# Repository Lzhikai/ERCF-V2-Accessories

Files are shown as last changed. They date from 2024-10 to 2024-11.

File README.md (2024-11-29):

# ERCF-V2-Accessories
 - [ERCF_v2-Official link](https://github.com/Enraged-Rabbit-Community/ERCF_v2)
 - [Siboor-ERCF_v2 kit Document link](https://docs.siboor.com/siboor-ercf-v2)  

## Announcement
In compliance with the latest requirements from the ERCF V2 team, the SIBOOR ERCF V2 GitHub repository will only host STL files created or modified by SIBOOR. For all other STL files, please download them from the official ERCF V2 platform.
To help our users better understand which STL files they need, we’ve prepared a concise guide. We hope it will be helpful to you!
Thank you for your support!  
https://docs.siboor.com/siboor-ercf-v2/the-build/1print-necessary-parts

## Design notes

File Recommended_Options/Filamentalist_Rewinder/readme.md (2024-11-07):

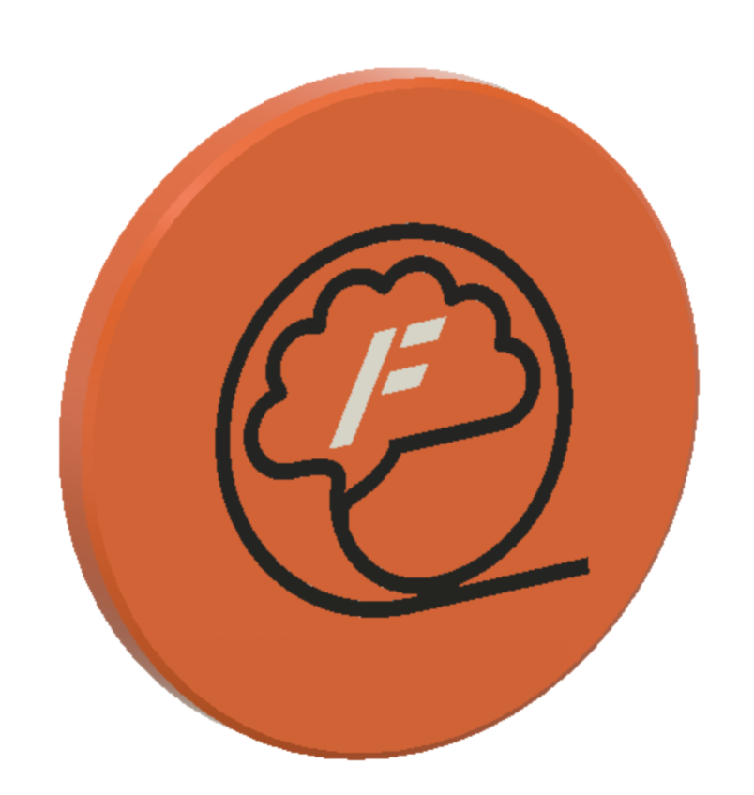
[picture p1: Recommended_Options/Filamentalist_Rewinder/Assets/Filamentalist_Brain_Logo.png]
<h1 align="center">The "Filamentalist"      Passive Filament Driven Rewinder</h1>
<p align="center">
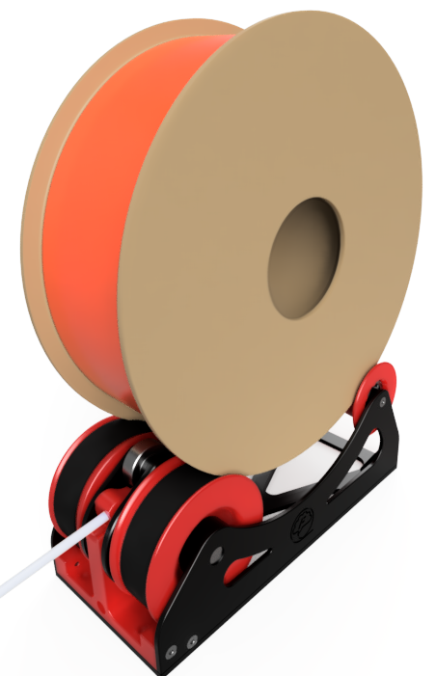
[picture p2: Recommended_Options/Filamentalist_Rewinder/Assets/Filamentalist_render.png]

</p>

## Filamentalist Discord group [here:](https://discord.gg/uDcGxukRKd) ##

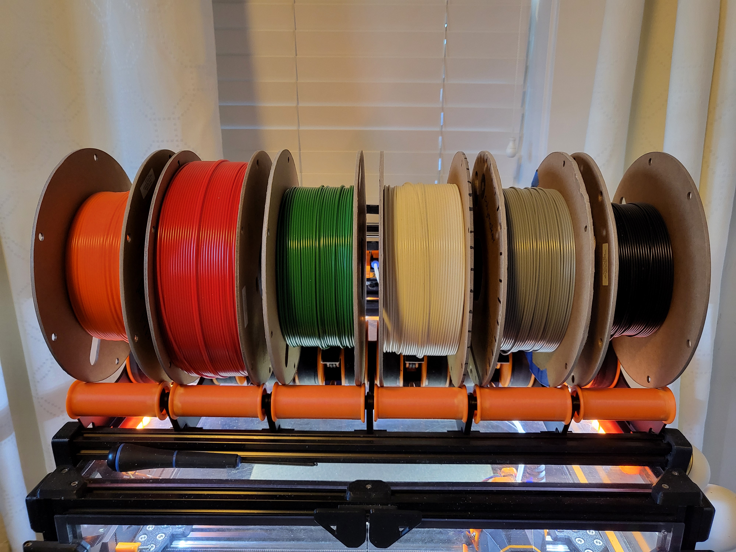
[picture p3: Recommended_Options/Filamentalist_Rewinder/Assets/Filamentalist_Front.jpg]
<p align="center">
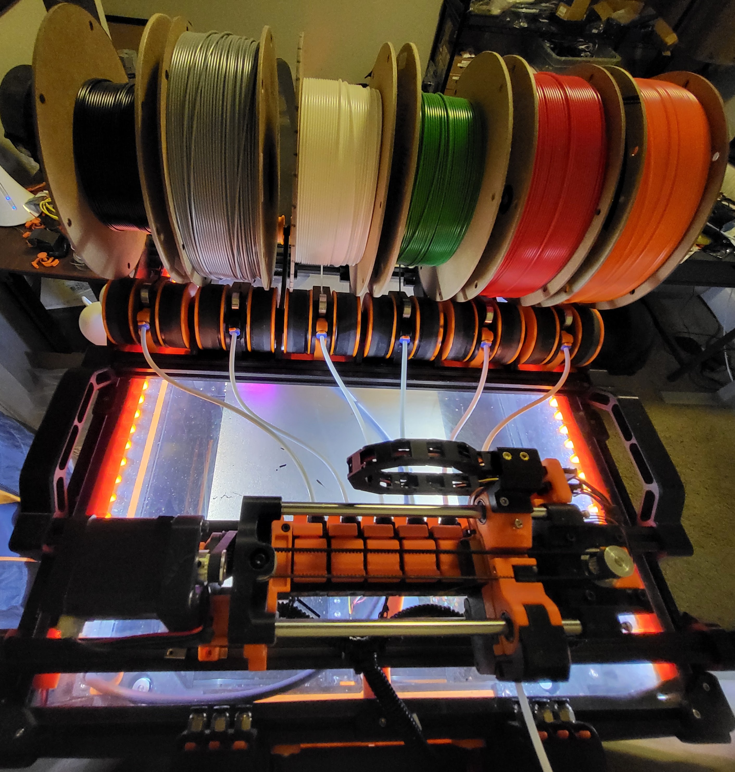
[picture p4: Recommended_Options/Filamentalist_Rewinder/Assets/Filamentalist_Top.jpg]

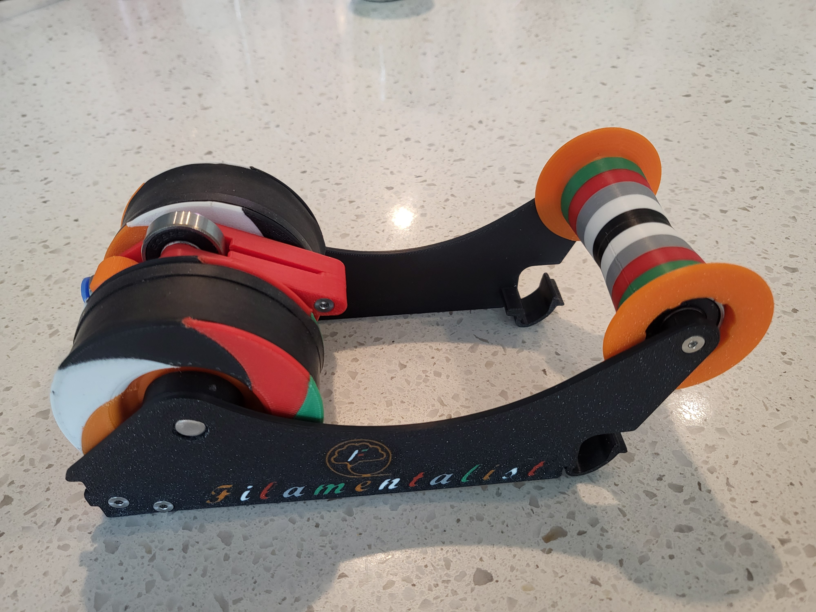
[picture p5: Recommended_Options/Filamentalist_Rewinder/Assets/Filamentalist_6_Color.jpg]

</p>

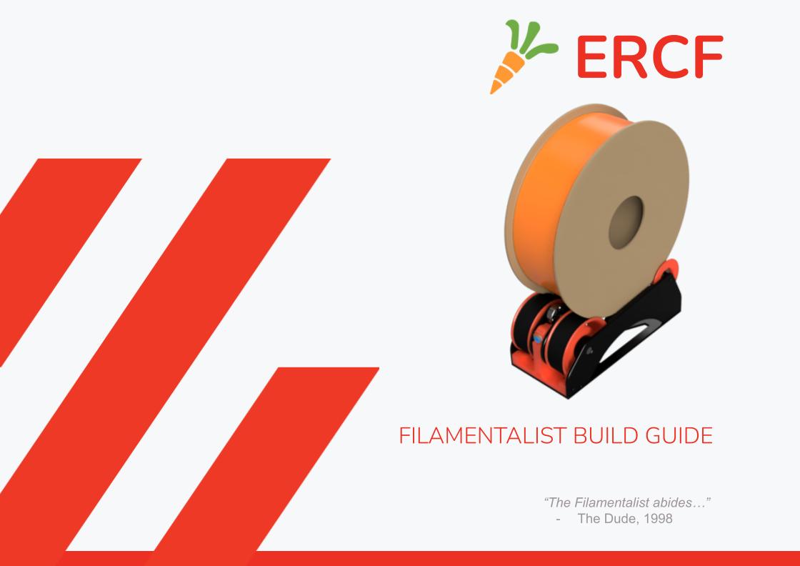
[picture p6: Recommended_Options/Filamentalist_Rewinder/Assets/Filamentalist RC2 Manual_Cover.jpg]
## [Filamentalist Assembly Guide Document](https://github.com/Enraged-Rabbit-Community/ERCF_v2/blob/b04e75d1da1841365e015c20a97aaef5a365349d/Recommended_Options/Filamentalist_Rewinder/Documentation/Filamental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)  [](https://github.com/Enraged-Rabbit-Community/ERCF_v2/blob/master/Recommended_Options/Filamentalist_Rewinder/Documentation/Filamentalist_Rewinder_Manual_V3.pdf)

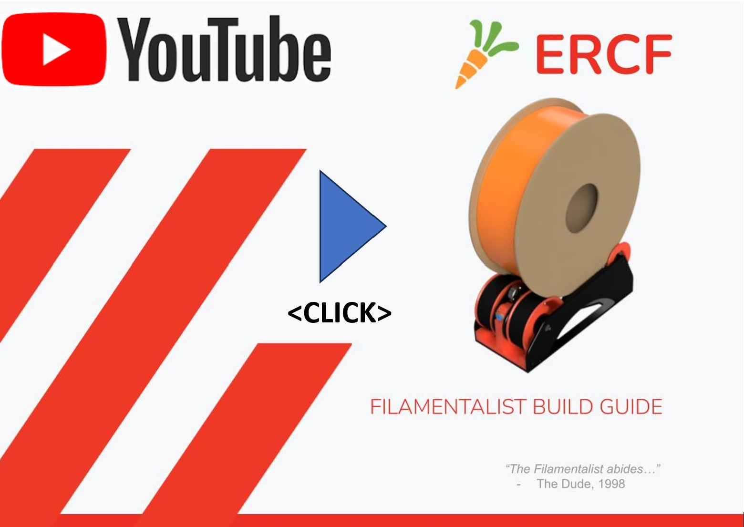
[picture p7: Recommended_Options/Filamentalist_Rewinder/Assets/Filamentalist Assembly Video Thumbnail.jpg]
## [Filamentalist Assembly Guide Video](https://youtu.be/-1cHOcnosxE?si=RZV318OI9f3f_CkE)  [](https://youtu.be/-1cHOcnosxE?si=RZV318OI9f3f_CkE)

## Video of 6 rewinders swapping (plus SW Only Blobifier Purging):  [](https://photos.app.goo.gl/hKso7JYPZcdRLKrW8)

## [Video of loading a spool (pre-gate sensors auto-detect filament and pull into ERCF):](https://photos.app.goo.gl/qPX1pxYLU2VeUuqV8)  [](https://photos.app.goo.gl/qPX1pxYLU2VeUuqV8)

## [Filamentalist Enclosure Drybox Project Github](https://github.com/SkiBikePrint/ERCF_Mods/tree/main/Filamentalist_Enclosure)
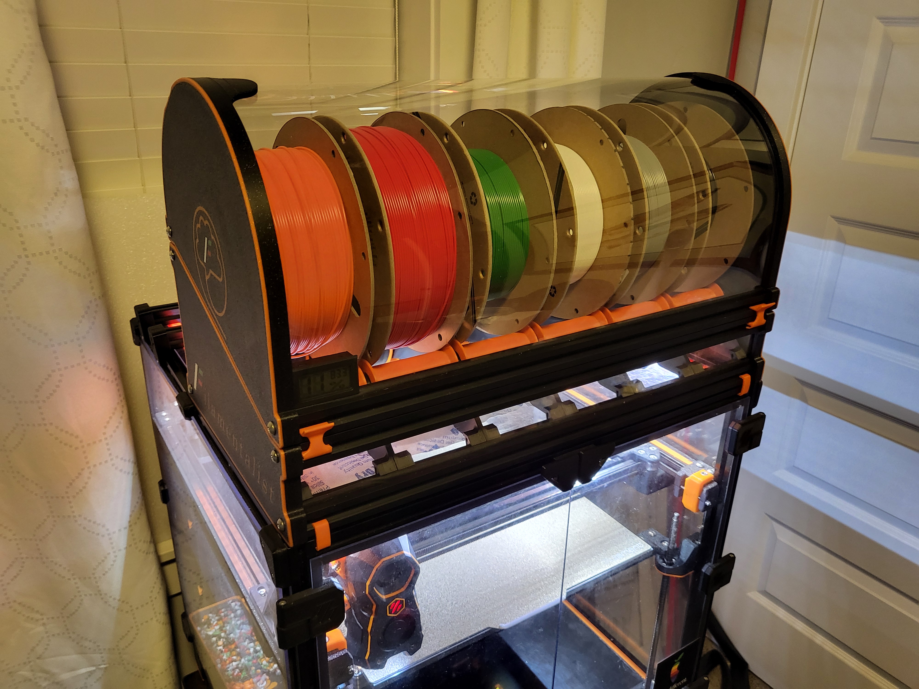
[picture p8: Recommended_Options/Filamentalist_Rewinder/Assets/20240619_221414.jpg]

</p>

##  Theory of operation:

The Filamentalist is an integrated solution for buffering and spool holding providing space savings as well as the potential for filament path reduction and the associated drag/resistance that comes with long runs from spool to buffer to MMU.

- The Filamentalist uses the axial force delivered by the MMU gear motor along the filament to load and unload to and from the filament spool.
- An adjustable spring clamp forces the filament against two o-rings that sit on the drive pulley to create a high traction interface for rotating the axle and filament spool.
- A one-way clutch style bearing locks against the drive shaft and rotates the filament spool to take up filament during an unload.
- For loading and print extruding, the clutch disengages allowing for effective free-spooling of the filament spool similar to a roller style spool holder.
- The difference in diameter of the filament driven clutched roller versus the larger roller that the filament spool sits on provides the needed gear ratio to produce enough rotations to take up, and unload a nearly empty or full filament roll.
- During unloading/buffering, to account for the varying diameter of a spool from full to empty filament tension will cause the spring loaded arm to lift a small amount and release traction from the o-rings allowing slip to occur between the filament and the o-ring interface of the rewinder (full spool = max slip, empty spool = no/minimal slip).

<p align="center">
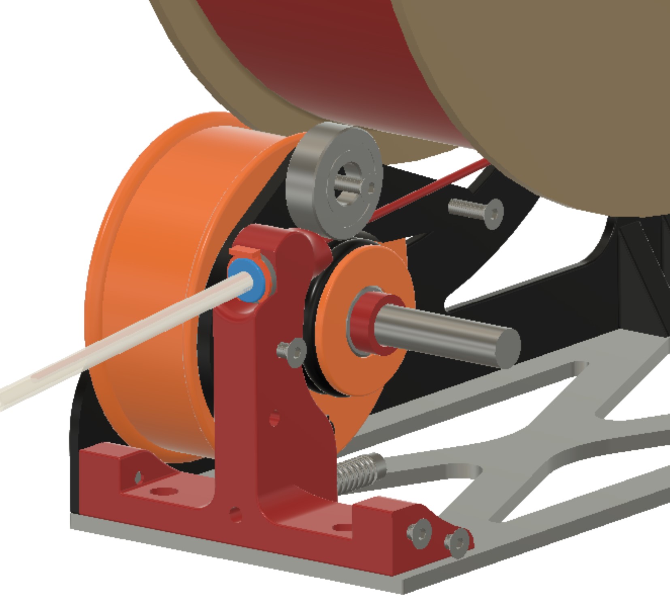
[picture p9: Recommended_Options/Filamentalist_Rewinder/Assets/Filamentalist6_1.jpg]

</p>

##  Credits:
Discord user Thisiscam first made me aware of [Muzi Xiaoyang's video](https://www.bilibili.com/video/BV1ZM41197fX/?spm_id_from=333.337.search-card.all.click) of a filament driven rewinder .  Through a long collaboration with Thisiscam, a great Beta dev/test team, and many design iterations/improvements on the Muzi Xiaoyang design, the Filamentalist was born. Key changes to the Muzi Xiaoyang design include incorporation of a one-way bearing, establishing the correct gear ratio for operation across the range of empty-to-full spools, and the long-life o-ring based filament clamping interface.

A special mention and thanks goes out to Cheesefrog and JCPhlux for their innovation and inputs for design refinement. 

##  **Additional Notes/Considerations** 

Things that you need to know include:
1. Due to continual evolution of the design based on user feedback, the pictures in this guide may not reflect the most current design.  They will be similar and generally represent the latest parts and assemblies .  The part names in the Printing Guidelines below will be kept current to match the CAD/STL files.
2. There are multiple options for the Filamentalist.  Determine which versions/options you want and select the stl's to print accordingly.
   - Unit Width: 80mm, 100mm, and custom width via Fusion 360 parametric model
     -  80mm - Designed around 80mm long off-the-shelf 8mm axles.  This standard version maximizes space efficiency with common spool size compatibility, accomodating spool widths up to 68mm.  Total rewinder width is 81.5mm allowing 6 units across the top of a 350 Voron mounted on 500mm extrusions.
     -  100mm - Designed around 100mm long off-the-shelf 8mm axles.  This size accomodates spool widths up to 86.5mm (basically all brands of 1kg spools).  Total rewinder width is 100mm.
     -  Parametric Model - If you use Autodesk Fusion 360 you can adjust the design for virtually any realistic spool width and axle size.  You can also "push" the design a bit using an acceptable axle "underhang" to get more spool width.  For example you can effectively accomodate a spool width of 72mm (KVP, NinjaFlex) on the 80mm axle with an underhang value of -2.75mm.  With this underhang the axle is still fully captured by the 608 bearings.  You could even push this further to an underhang of -5.75mm to get a max spool width of 78mm and still have acceptable axle engagement with the 608 bearings.
   - Mounting Style: Standard (shelf) mount, 2020 rail clip-in mount, 2020 clip-in mount for Filamentalist Enclosure
       - Based on your mounting needs, you may or may not need to print and install the Base Plate part.  It is really only needed if you don't plan to attach the rewinder to a surface.
   - Feed Direction: The orientation of your MMU with respect to your filament spools location may require a front, rear, or bottom loading capability from the
       rewinder.  Tensioner Mount options are provided to support this.
   - Pre-gate Sensors: If your MMU does not have pre-gate sensors and the software you use supports them (like Happy Hare) there are Tensioner Mount options that  support this.
3. If you're using, or upgrading from a ERCFv1 or v2 RC1A version you may want/need a higher torque gear motor.  Many in the Beta team ran NEMA 17's spec'd at 55 N-cm max torque and config'd them for 1-1.5A (probably overkill...).  Grafton's [40 Tooth NEMA 17 Mod](https://www.printables.com/model/692720-ercf-40-tooth-gear-modifiction) is a good addition for gaining more speed from a high torque motor.  This may not be required so if you already have built your ERCF, try the Filamentalist with the motor/gearing you have and decide if you think you need more torque/speed.
4. One baseline width of the Filamentalist is set to use a 80mm axle length.  It has a maximum spool width of 68mm and supports most standard 1, 0.5, and 0.25KG spool sizes and still be able to fit 6 rewinders across the top of a 350 size Voron printer. Height was set to be as low as possible to fit some existing dry box designs although there is the possibility to make user modifications to to reduce height further if needed. Some spools such as NinjaFlexand KVP's are too wide to fit the 80mm design.  If you use spools wider than 68mm there is also step and stl files posted for a 100mm axle length version. If you are using Autodesk Fusion 360 the provided .f3d file in the CAD directory is a parametric based model allowing you to customize the width of your rewinder to suit your max/min spool widths and/or to design around a standard available steel axle length (see instructions here  [parametric_model](https://github.com/Enraged-Rabbit-Community/ERCF_v2/blob/master/Recommended_Options/Filamentalist_Rewinder/CAD/readme.md) ). 
5. Because the standard tuning of this design relies on some filament slip at the o-rings, the o-rings may ultimately wear-out.  Testing and extrapolation estimates that the wear-out point is ~5K cycles. See the O-Ring Replacement section at the end of this document for o-ring swap/replacement instructions. 
6. Due to pressfits for the 608 bearings and ECAS fitting printer calibration is important.  A "Test Block" stl is included.  It is recommended you print this first and test the press fits and measure the two small holes (2.7mm for cutting 3mm screw threads and 2.3mm for the filament path) to determine if you need to apply any scaling or changes to your extrusion factors in your slicer before printing.  Due to varying ECAS supplier tolerances and varying printer tolerances some experienced cracking at the ECAS hole when pressing in the ECAS.  If all other press fits work well on the Test Block but you experience cracking at the ECAS hole when pressing in an ECAS fitting, you can use an Xacto knife to lightly remove some plastic from the ECAS hole.  If the ECAS is too loose you can use superglue to glue the ECAS into the Tensioner Mount (not the Test Block 😉 ).
7. Questions or input?
   - Refer to the [FAQ](https://github.com/Enraged-Rabbit-Community/ERCF_v2/blob/master/Recommended_Options/Filamentalist_Rewinder/Filamentalist_FAQ.md)
   - [Troubleshooting Guide](https://github.com/Enraged-Rabbit-Community/ERCF_v2/blob/master/Recommended_Options/Filamentalist_Rewinder/troubleshoot.md)
   - Filamentalist Discord group [here:](https://discord.gg/uDcGxukRKd)

##  **BOM:**

**ATTENTION!! PLEASE READ COMMENTS IN FAR RIGHT COLUMN** (you may need to scroll over in your view)

| Qty per Site | Part | Example Source Reference | Comments |
|---|---|---|---|
| 1 | 8mm dia. x 80mm Stainless Steel Dowell Pin | https://www.amazon.com/uxcell-Stainless-Chamfered-Support-Elements/dp/B0BC8VFSWD, Amazon Alternate https://www.amazon.com/Unifizz-Stainless-Steel-Round-Silver/dp/B09P9MC953?th=1 (sheared ends may need to be cleaned up), Aliexpress https://www.aliexpress.us/item/3256801518620991.html | Undersized shaft (7.93-7.97mm or 5/16" dia) works the best.  100mm length is more available and can extend out of rewinder, you can cut polished 8mm or 5/16" diameter stainless rod to length, or there are stls to make a wider rewinder based on a 100mm axle.  Custom rewinder widths are also possible using the Fusion 360 parametric model and you can cut shaft to whatever length is desired. 8mm (or 5/16") diameter straight stainless tube is also an excellent alternative to solid rods as the are much easier to cut to length. |
| 5 | MR608 bearings | Can be obtained anywhere (Home Depot, Amazon, Aliexpress, etc.)  | MR608-2RS style recommended, but open or  MR608-ZZ style will work |
| 1 | HF081412 One-Way Bearing | https://www.amazon.com/dp/B0C7TRFJBS, Aliexpress | 8mm Bore, 12mm length, 14.2mm Diameter. Get the "octogonal" style. |
| 1 | ECAS press-in pneumatic fittings for the bowden tubes (like used in ERCF)  |  | A locking clip is required and can be bought or printed (stl included).  The rubber seal is not needed and should not be installed upon assembly. |
| 2 | O-rings | Metric 3.5x20 (ID) or AS568 Standard size 211, Home Depot #110, Amazon example: https://www.amazon.com/211-Buna-N-Ring-Durometer-Black/dp/B000FN0W7I/, Aliexpress example: https://www.aliexpress.us/item/2255799953260685.html (select correct size) | In the range of 13/16" ID, 1-1/16" OD or ~20mm ID, ~27mm OD, ~3.5mm cross section/cs, Nitrile Butadiene Rubber (NBR or Buna-N)|
| 1 | Spring  | https://www.amazon.com/dp/B076LNJF5Q, Aliexpress | Like in extruders - 304 Stainless Steel,6mm OD,0.6mm Wire Size,7.5mm Compressed Length,15mm Free Length (the stiffer 1mm wire size extruder spring used on CW2 and G2E will also work if you have those on-hand) | |
| 1 | 3mm Heatset Insert | M3x4x5 like these:  https://www.amazon.com/gp/product/B09MCW7ZN5 | Voron standard size | set into the Tensioner Mnt |
| 1 | 3x35mm SHCS | SS Socket Head Cap Screw | Spring Tensioner Screw anything in the range of 35mm +/- 10mm should work.  If building the alernate reverse access version then a 30mm length is recommended. |
|  2-6  | M3x10 SHCS  |  Stainless Steel Socket Head Screw | for locking rim rollers to 8mm steel axle shaft.  1 to 3 screws per roller Depending on tightness/looseness of Rim Roller center bore |
| 6 | 3x12 FHCS  |  Stainless Steel Flat Head Screw | for Tensioner Mnt and Rear Axle installation 8/10/12mm lengths will work|
| 3 | 3x18 FHCS  |  Stainless Steel Flat Head Screw | for Tensioner Arm clamp bearings and Tensioner Mnt pivot installation 16mm length will work |
| 1 | M3 Washer  |  Stainless Steel | between Spring Tensioner screw head and spring |
| 2 | Rubber Band | See [FAQ](Filamentalist_FAQ.md) | bike tire inner tube or rubber bands |

**Optional Parts**
| Qty per Site | Part | Example Source Reference | Comments |
|---|---|---|---|
| 1 | D2F-L3 Microswitch  | Omron brand - Mouser, Digikey, etc., Aliexpress example: https://www.aliexpress.us/item/3256805036222979.html  | for pre-gate sensor option versions |
| 2 | M2x10 Self Tapping Screw | Philips or socket head.  Amazon example: https://www.amazon.com/DTGN-M2x10mm-Phillips-Self-tapping-Screw/dp/B0CSRTYBLR, Aliexpress example: https://www.aliexpress.us/item/3256802486141312.html (select size) | for pre-gate sensor option versions |
| 1 | JST-XH 2-pin Socket/Plug | Amazon example:  https://www.amazon.com/CQRobot-Connector-Terminals-Housing-Adapter/dp/B0B2R966ZY, Aliexpress Example: https://www.aliexpress.us/item/3256804799083128.html (need housing, plug, and terminal) | for pre-gate sensor option versions |
| var. | 24 awg wire  | | for pre-gate sensor option versions |
| var.  | 2.5mm ID PTFE tubing | Amazon, Aliexpress, 3D printing vendors | 2.5mm ID recommended but you can try whatever you have.  Length depends on the distance from your rewinder location to your ERCF inputs |

##  Printing Guidelines:

## **General:**
- Material: ABS or ASA (~170 gm per site)
- Print Time: ~8hr 17min (based on the Ellis PIF profile speeds, accelerations, and volumes)
- 0.2mm layer height
- 40% infill recommended.  Linear style infills are fastest (rectilinear, monotonic, grid, triangles, stars, etc.)
- Wall Count: 4
- Solid Top/Bottom Layers: 5

## **Part Specific:**
- Orientation suggestions are relative to the installed assembly orientation and are shown in the slicer images below.
- There are stls for both 80mm and 100mm wide version and a Fusion 360 parametric CAD model for additional custom widths.  See "Additional Notes/Considerations" point 3 above for more details.
- If rotating the Filamentalist is not feasible for your required filament loading direction or you need a bottom feed capability (for example enclosure limitations or feeding through the bottom of a shelf) there is an option for a rear loading version which only requires printing the Tensioner_Mount_Rear_Load_80mm/100mm_[option] in the place of Tensioner_Mount_80mm/100mm part.
  
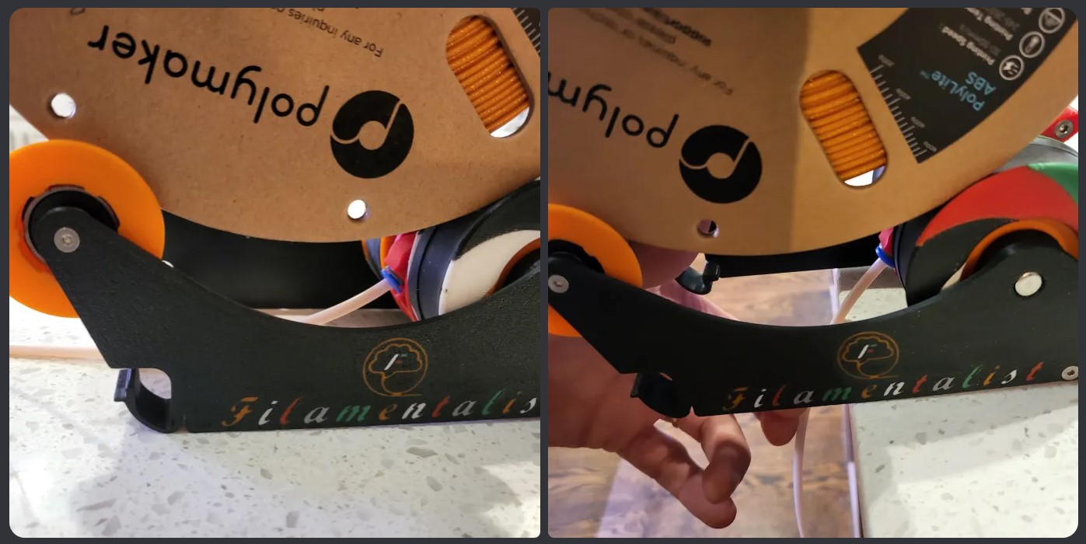
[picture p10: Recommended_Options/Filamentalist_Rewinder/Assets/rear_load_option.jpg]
  

- Stl's are provided for optional clip-in style supports where no Base_Plate is needed and the rewinders are easily clipped in and out of (2) 2020 extrusions mounted 170mm center-to-center apart.  This option is highly recommeded if your setup can accomodate this style type of mount.
  
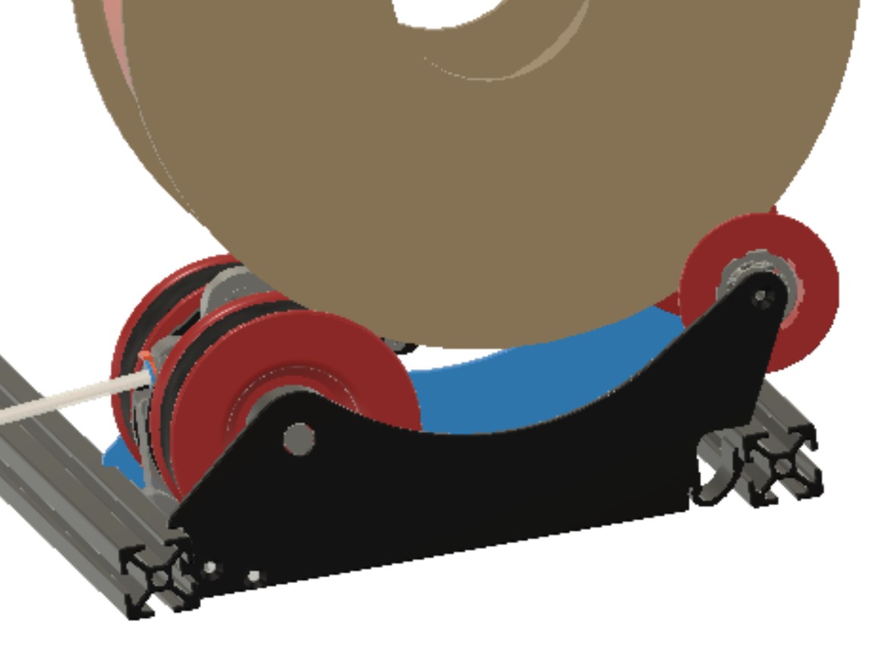
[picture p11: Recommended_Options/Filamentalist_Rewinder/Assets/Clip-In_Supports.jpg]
  
- **!! IMPORTANT !!  This design relies on multiple press-fits for bearings and ECAS fittings.  As a result, printer calibration is important.  A Test_Block stl is included.  It is highly recommended that you print this block first, check fits, and make adjustments to extrusion multipliers and/or slicer scaling if needed before printing the Filamentalist parts.**
  
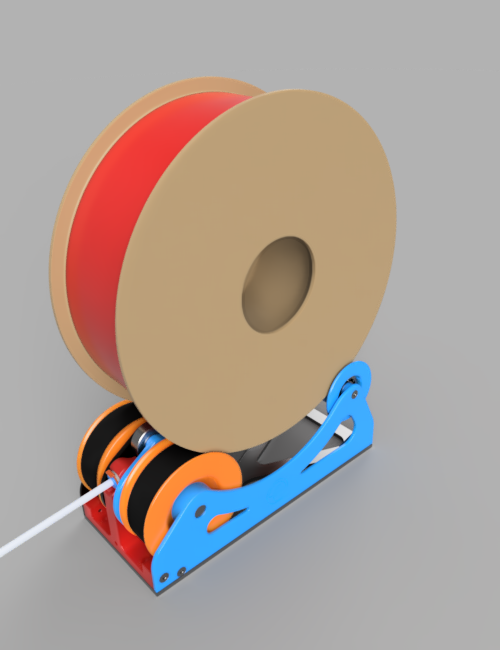
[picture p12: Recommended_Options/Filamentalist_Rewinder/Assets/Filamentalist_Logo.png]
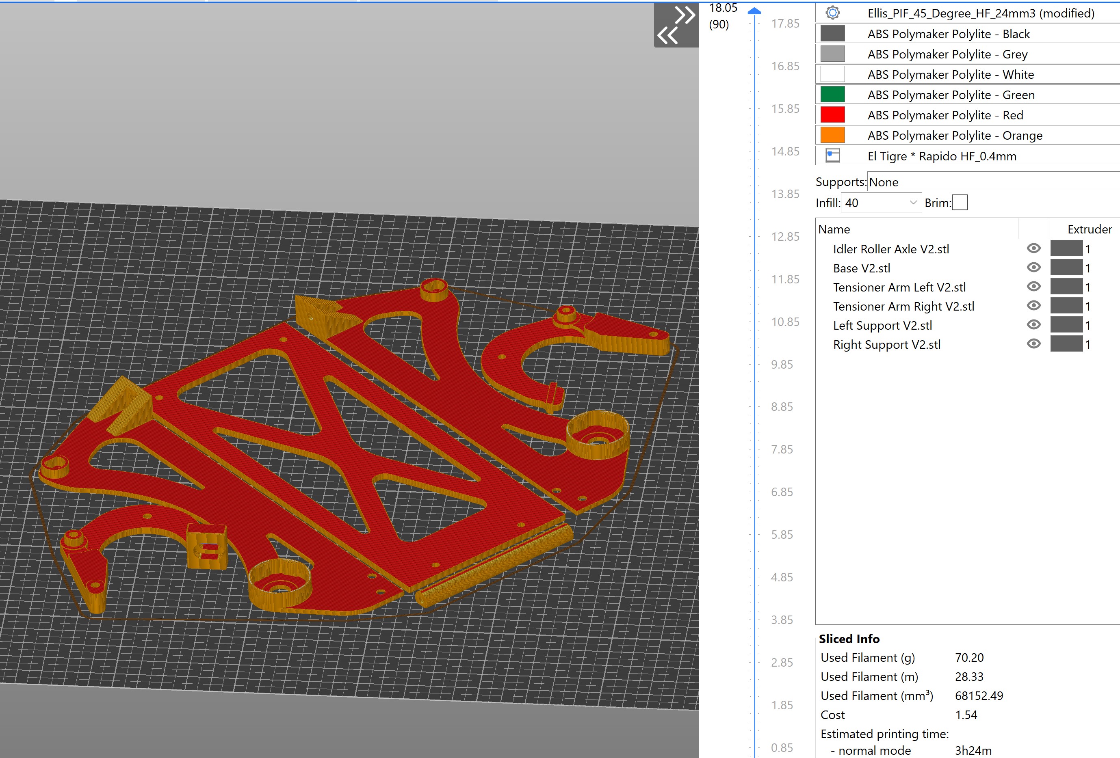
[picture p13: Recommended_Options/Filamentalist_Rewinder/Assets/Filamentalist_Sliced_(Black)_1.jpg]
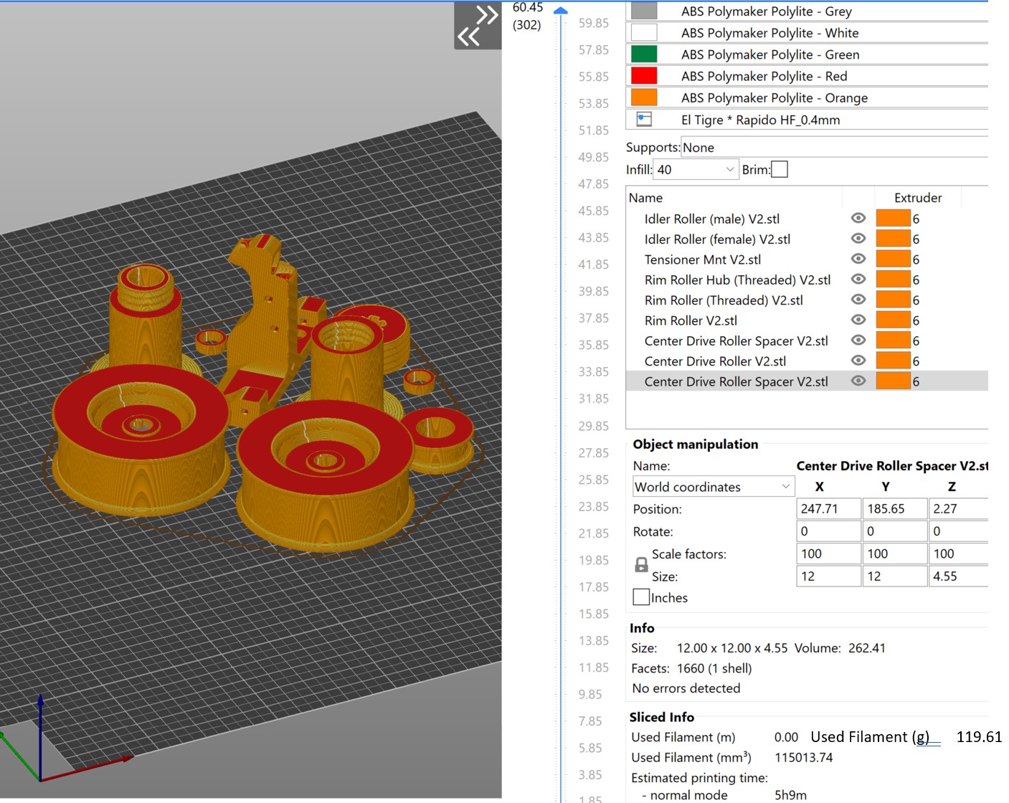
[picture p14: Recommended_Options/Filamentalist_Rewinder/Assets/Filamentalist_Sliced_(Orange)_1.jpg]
    

| **Qty per Site** | **Part**  | **Pic** |  **Orientation** | **Printed Supports Needed** | **Comments** |
|---|---|---|---|-----|---|
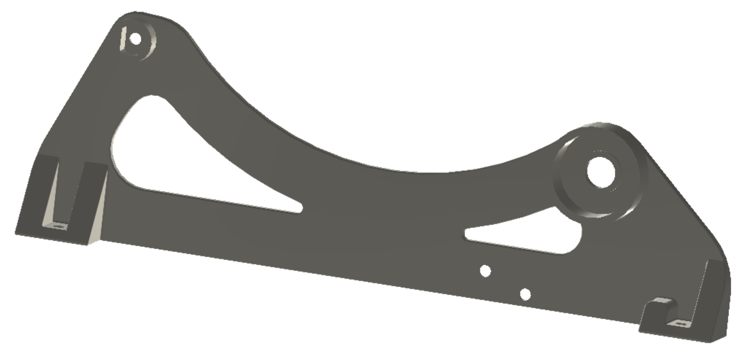
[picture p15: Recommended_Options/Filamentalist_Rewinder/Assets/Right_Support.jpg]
| 1 | Right_Support |  |  Horizontal | N | |
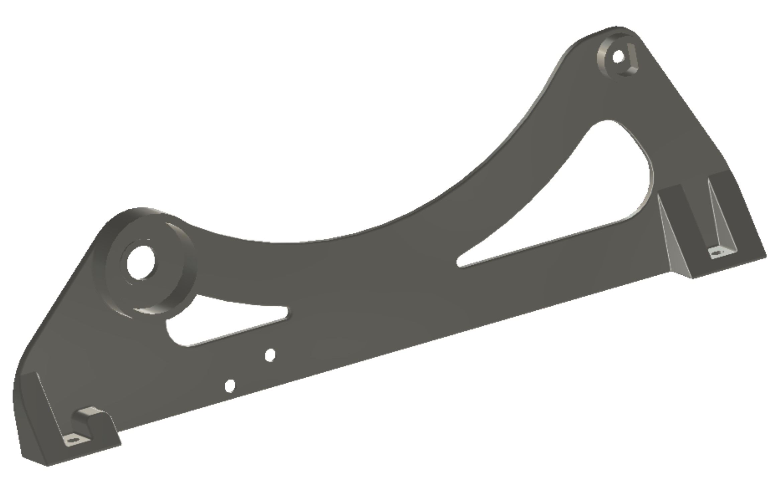
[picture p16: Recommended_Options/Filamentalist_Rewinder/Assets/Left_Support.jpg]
| 1 | Left_Support |  | Horizontal | N | |
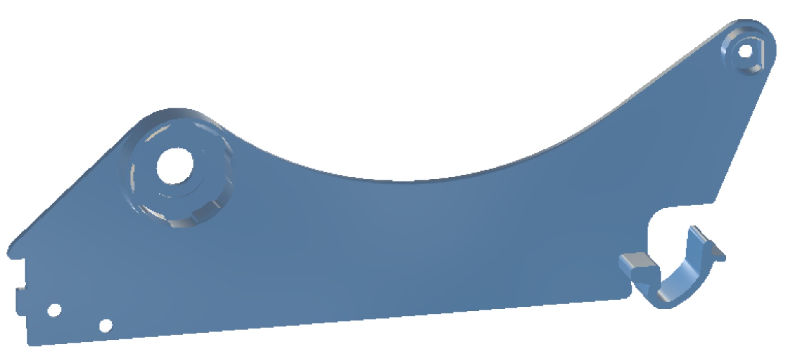
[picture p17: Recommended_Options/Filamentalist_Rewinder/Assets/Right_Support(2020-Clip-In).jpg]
| 1 | Option: Right_Support_[2020_Clip-In_option] |  |  Horizontal | N | |
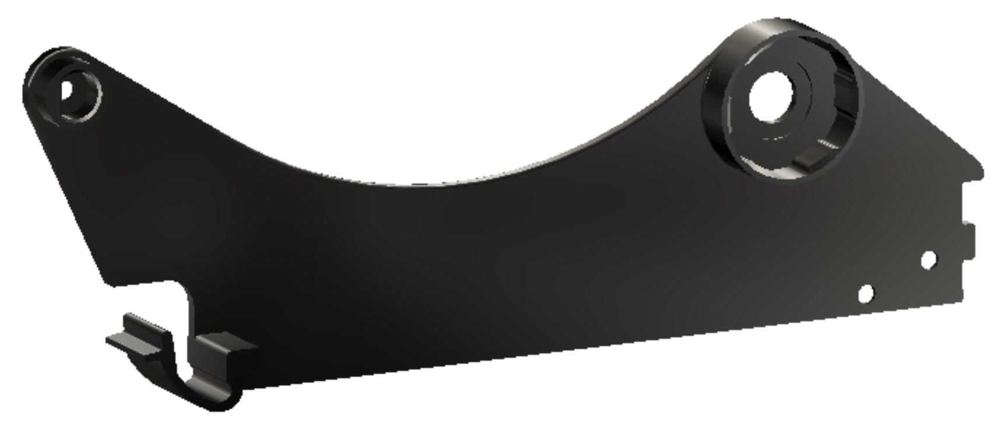
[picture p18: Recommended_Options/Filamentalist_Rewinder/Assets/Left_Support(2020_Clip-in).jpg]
| 1 | Option: Left_Support_[2020_Clip-In_option] |  | Horizontal | N | |
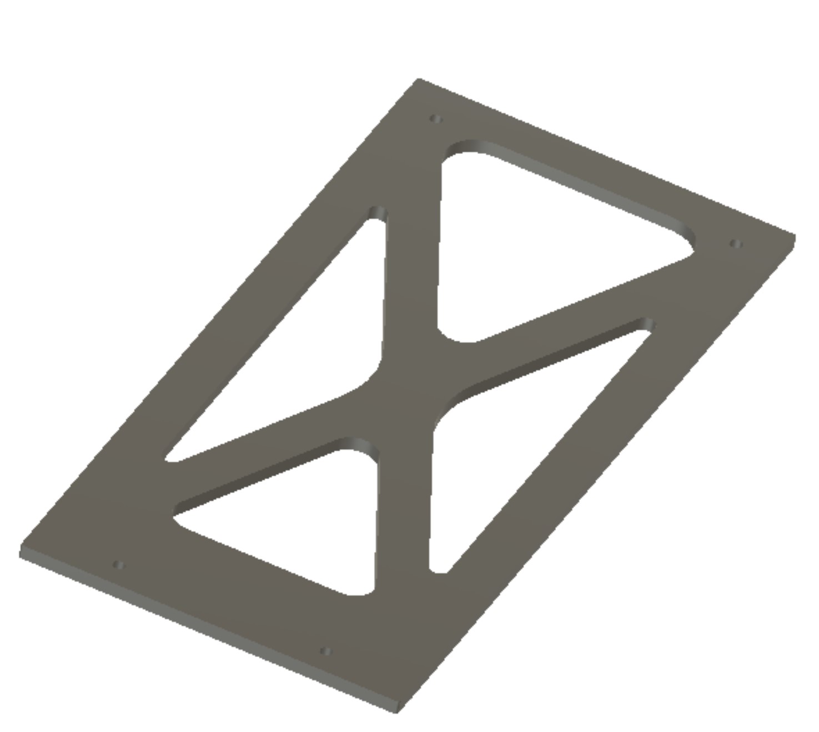
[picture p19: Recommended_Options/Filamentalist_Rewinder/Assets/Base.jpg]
| 1 | Base_Plate_80mm/100mm_[option] |  | Horizontal | N | Optional part for a standalone unit not mounted to another surface  |
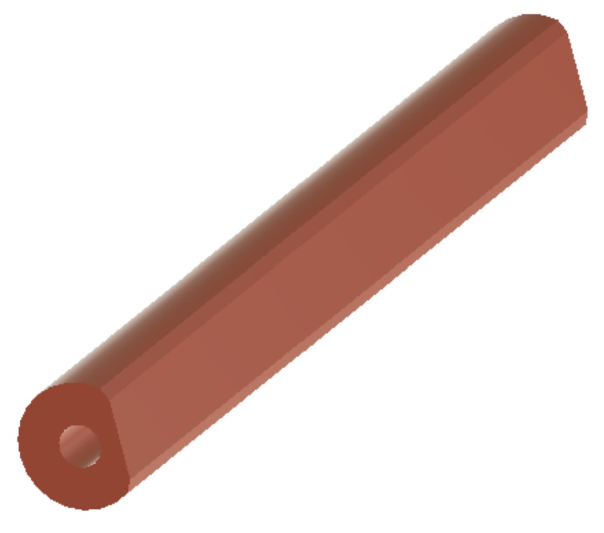
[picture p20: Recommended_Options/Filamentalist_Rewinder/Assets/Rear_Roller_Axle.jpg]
| 1 | Idler_Roller_Axle_80mm/100mm  |  | Horizontal | N | align flat of "D" to build plate |
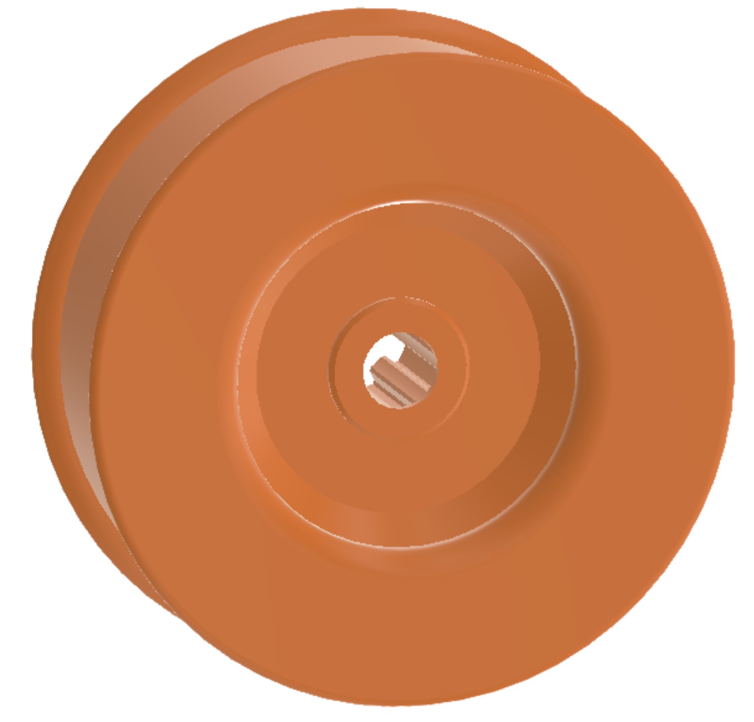
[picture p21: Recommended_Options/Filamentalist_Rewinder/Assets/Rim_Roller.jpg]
| 2 | [a]_Rim_Roller_80mm/100mm |  | Horizontal | N | Dished side up. |
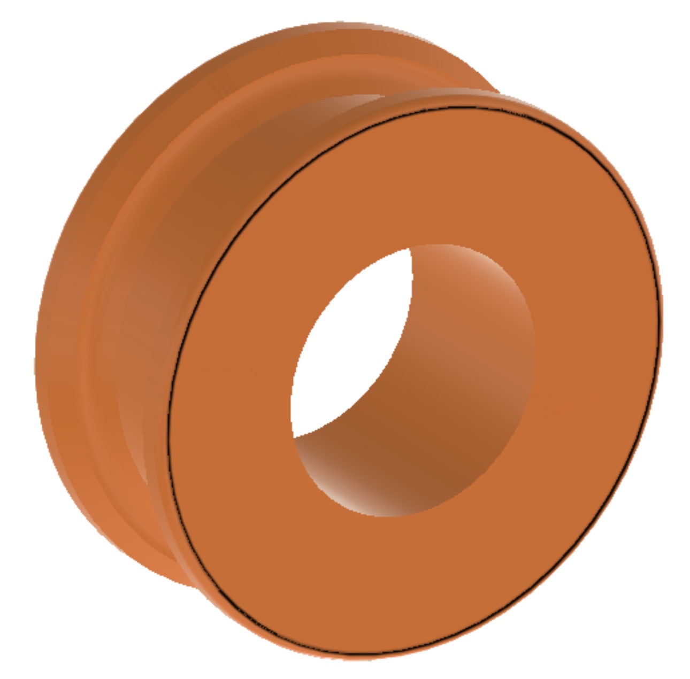
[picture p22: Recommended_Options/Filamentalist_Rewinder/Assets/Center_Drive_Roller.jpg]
| 1 | [a]_Center_Drive_Roller  |  | Horizontal | N | Recommend scattered seams for press fit-bore concentricity |
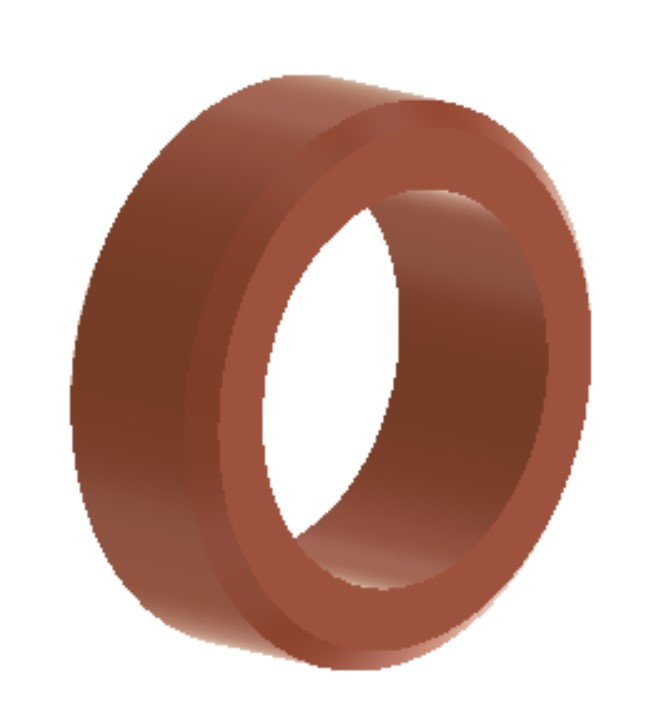
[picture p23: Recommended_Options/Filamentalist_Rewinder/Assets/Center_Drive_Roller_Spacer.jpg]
| 2 | CDR_Spacer_80mm/100mm |   | Horizontal | N | |
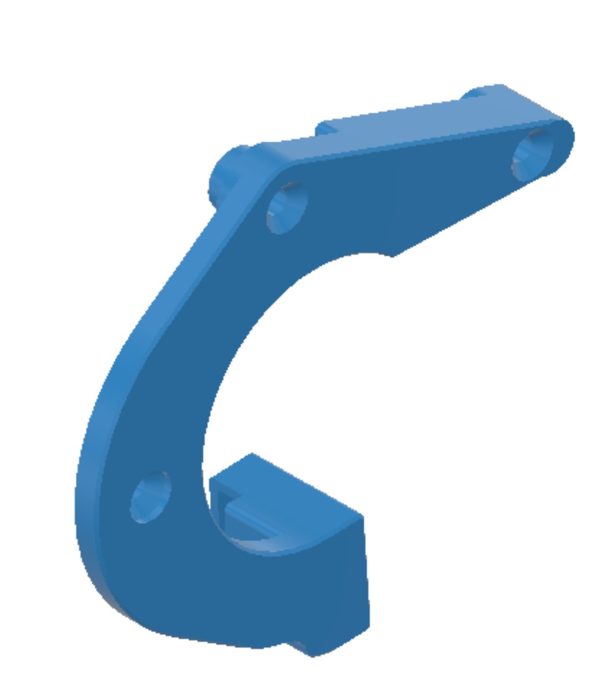
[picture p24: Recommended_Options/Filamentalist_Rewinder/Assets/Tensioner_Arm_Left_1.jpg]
| 1 | Tensioner_Arm_Left |   | Horizontal |  N |  |
| 1 | Tensioner_Arm_Right |   | Horizontal |  Built-in | Remove built-in support from the locking tab |
| 1 | [a]_Tensioner_Mount_80mm/100mm |  | Vertical (as installed) | N  | There is a pre-gate sensor option version available as well (split to parts in slicer for print-in-place breakaway connector retaining key).  |
| 1 | [a]_Tensioner_Mount_Rear_Load_80mm/100mm _[option] |  | Vertical (as installed).  Optional for rear loading if needed. | N  | There is a pre-gate sensor option version available as well.  |
| 1 | [a]_Idler_Roller _(male) _80mm/100mm |   | Vertical  | N  |  Scattered seams |
| 1 | [a]_Idler_Roller _(female)_80mm/100mm |   | Vertical  | N  |  Scattered seams |
| 1 | Axle_Depth_Tool_80mm/100mm |  | Vertical | N | Pocket opening up.  Print with 100% infill for reuse strength and durability when building multiple rewinders. |
| 2 | [a]_ECAS_Clip |  |  Horizontal | N | Tab up |
| 1 | Test_Block |  |  608 Pocket facing up | N | printer calibration tool |

##  [Assembly Manual](https://github.com/Enraged-Rabbit-Community/ERCF_v2/blob/master/Recommended_Options/Filamentalist_Rewinder/Documentation/Filamentalist_Rewinder_Manual_V3.pdf)  [](https://github.com/Enraged-Rabbit-Community/ERCF_v2/blob/master/Recommended_Options/Filamentalist_Rewinder/Documentation/Filamentalist_Rewinder_Manual_V3.pdf)

## [Filamentalist Assembly Guide Video](https://youtu.be/5Qk3N2sKz40)  [](https://youtu.be/5Qk3N2sKz40)

##  Tuning

Tune by setting the Tensioner Arm clamping force.  The arm does not need an extreme amount of tension.  To tune the spring force, lift the tensioner and insert a section of filament through the o-ring bearing interface and into the bowden tube.  Hold the center roller by placing your thumb against the o-rings and try to pull the filament out.  You want the slip force to be slightly more than what the overall system drag is, so you have to imagine the range of gear motor pull force vs rewinder drag and set a slip range in-between the two "imaginary" lines.  Adjust the spring tensioner screw accordingly and err on the light side.  Run the rewinder (see test code below). If loose filament is forming around the filament spool during unload, tighten the spring tensioning screw.  If no loose filament is forming around the filament roll, gradually reduce the spring tension until loose filament starts to accumulate and then increase tension in ~1/2 screw turn increments until you feel you have the lightest tension that results in a tightly packed unload. 

##  O-Ring Replacement

You may never need to replace o-rings.  Testing and extrapolation estimates that the wear-out point is ~5K cycles.  The impact of o-ring wear-out can be reduced by periodically swapping highly used rewinders with low use rewinders in your line-up.  Also, o-rings with grooves worn in them can be swapped with their opposing partners to present the unworn side/face to the filament to extend the life of a set.  For o-ring replacement, remove the Drive Roller Assembly from the rewinder (unscrew the (6) screws of the Right and Left Supports).  Then unscrew the set screw on one Rim Roller.  You can now slide the CDR Spacer and Center Drive Roller from the axle, remove the old o-rings (a dental pic works great), and install a pair of new ones.  Reinstall the Center Drive Roller and CDR Spacer back on the axle and install the Rim Roller back onto the axle per 3.3 above, and re-install the supports.  

##  Troubleshooting

Please see [troubleshooting guide](troubleshoot.md), reference the [FAQ](Filamentalist_FAQ.md), or join our discord server (https://discord.gg/uDcGxukRKd) for more help.

##  Testing

Below are macros you can cut and paste into the bottom of your mmu_software.cfg or printer.cfg to test and tune your rewinders.

Happy multi-material printing and rewindering!

```
[gcode_macro rewinder_test]
gcode:
    MMU_TEST_LOAD LENGTH=50
    {% for n in range(20) %}

# cycles currently set at 20, i.e. range(20).  You can changes this however you chose.
        MMU_SERVO POS=DOWN
#        MANUAL_STEPPER STEPPER="gear_stepper" SPEED=300 ACCEL=400 MOVE=800
        MMU_TEST_MOVE SPEED=300 ACCEL=400 MOVE=800
# change the SPEED and ACCEL as you see fit
        MMU_SERVO POS=UP
# to stop a macro mid-cycle you must use the e-stop.  This dwell allows you to hit the e-stop while the servo is up so that you can pull the filament out of the ERCF while the printer/macro is stopped
        MMU_SERVO POS=DOWN
        MMU_TEST_MOVE SPEED=300 ACCEL=400 MOVE=-800
        MMU_SERVO POS=UP

    {% endfor %}

[gcode_macro rewinder_test_multitool]
gcode:
    {% set gates = [5] %} # [0,1,2,3,4,5] move between these gates
    {% set test_load_length = params.TEST_LOAD_LENGTH | default(50) | float %}
    {% set repeats = params.REPEATS | default(20) | int %}
    {% set speed = params.SPEED | default(300) | float %}
    {% set accel = params.ACCEL | default(400) | float %}
    {% set length = params.LENGTH | default(800) | float %}

    MMU_HOME

#    MMU_TEST_LOAD LENGTH=50
    {% for n in range(repeats) %}
        {% for gate in gates %}
            MMU_SELECT GATE={gate}
            MMU_TEST_LOAD LENGTH={test_load_length} # preload gate for a bit of length
            MMU_TEST_MOVE SPEED={speed} ACCEL={accel} MOVE={length}
            MMU_SERVO POS=UP
            MMU_TEST_MOVE SPEED={speed} ACCEL={accel} MOVE=-{length}
            MMU_EJECT
            MMU_RECOVER

        {% endfor %}
  
    {% endfor %}
```

#  Version History

Versioning convention.  V"X"."Y"."Z"
- "X" represents a major change in form, fit, or function.  An increment in "X" may not require that existing built units undergo rework but the new parts will generally not be compatible with past version rewinders.
- "Y" represents a "step rev" or minor revision.  These are generally small "tweaks" for improved functionality, useability, and/or assembly and typically would not require reprint/rework for existing rewinders.  
- "Z" represents a backwards compatible "bug fix".  This will generally be addressing nuisance CAD or printability issues.

V1 - 5/17/24 - Public release into ERCF V2 RC2 repository

V1.1 - 5/19/24 - Update to CAD and stls for Tensioner Arms to remove potential filament catching point during endless spool ejection

V1.2 - 5/20/24 - Reverted Center_Drive_Roller to cylindrical press fit hole (vs hex of V1 and V1.1).  Revised 608 press fit pockets of Idler_Roller_(male&female) parts for both 80mm and 100mm width versions for improved press fit.

V1.3 - 5/20/24 - Added bevel to internal step on  Idler_Roller_(male) part for 80mm and 100mm versions to improve printability.  Updated the .f3dparametric file, step files, and stls for 80mm and 100mm versions.

V1.4 - 5/21/24 - Shortened threads on Idler_Roller_male parts by 1.5mm to remove slight interference.  Updated CAD, 80mm, and 100mm stls.

V1.5 - 6/4/24 - Slightly deepened 608 bearing pockets in Idler Roller parts to prevent potential side loading binding due to print/assembly tolerances.  Reprint not required for existing functioning units.

V1.6 - 6/12/24 - No mandatory reprints/rebuilds required:  Updated CAD parametric model and 80/100mm step files because two  Tensioner Mount-to-Support holes were getting "buried" in the 100mm version.  Updated the Tensioner_Mount_100mm stl file as well.

V1.7 - 6/13/24 - Opened up c-sunk hole on Tensioner_Arm_Left part pivot screw hole to allow for full seating of a FHCS head and use of a 16mm long screw.  A new stl for Tensioner_Arm_Left ans new f3d and step files are included.

V1.8 - 7/2/24 - Removed notch/gap in axle pressing tool that shouldn't have been there.  80/100mm stl's updated as well as f3d and stp CAD files.

V2 - 7/22/24
  1. Added Rear Load option Tensioner_Mount (works as bottom load too)
  2. Removed threaded Rim Roller option and converted Rim Rollers from press-fit to set screw style.
  3. Add 608 bearing inner race clearance back into Supports.
  4. Added ~2mm of additional bowden capture in Tensioner_Mounts

V3 - 8/5/24
  1.  Add options for Tensioner Mounts with pre-Gate sensors
  2.  Included option for the Filamentalist Enclosure style Base Supports
  3.  Updated all supports to include a spool guide rail to help keep spools from wandering off of the rollers.

V3.0.1 - 8/8/24 - No reprint/rebuild required:
1. Improved clearances for indexing tab feature in Tensioner Arm parts
2. Improved breakaway feature for small print-in support in Tensioner_Arm_Right part 
3. Provided additional edge chamfering to Idler Roller Axles
4. Reinstated design history in Filamentalist_(parametric)_V3.f3d CAD model so that the parametric functionality would work correctly.
5. Added accent color to file naming convention in stl file names.
6. Updated pdf manual to reflect/describe accent color for file naming convention in stl file names.

V3.0.2 - 8/15/24 - No reprint/rebuild required:
1. Added more reference dimensions to the User Parameters section for the Filamentalist_(parametric).f3d parametric CAD model.
   
# To DO

1.

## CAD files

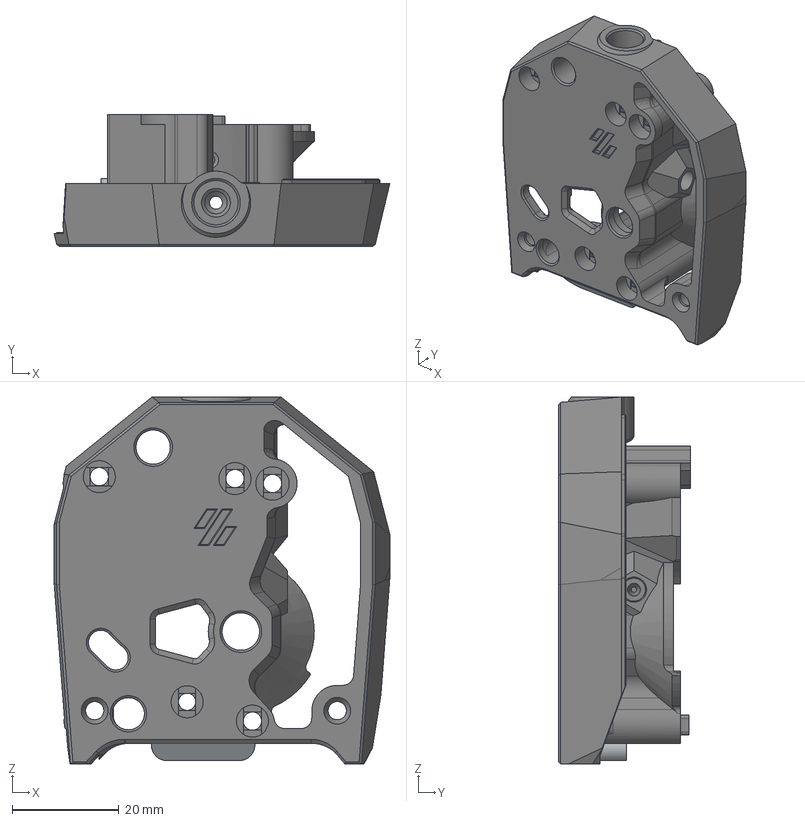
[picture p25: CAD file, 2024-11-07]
Recommended_Options/ERF_Filament_Cutter/CAD/SB_CW2_Main_Body_Cutting_With_ECAS.step
62.8 x 24.7 x 68.7 mm

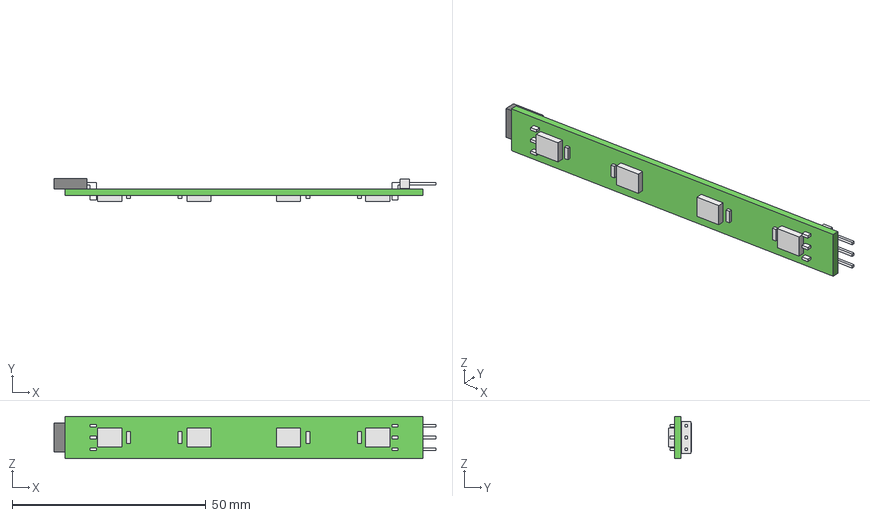
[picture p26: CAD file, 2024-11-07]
CAD/Misc/Apron_Neopixels/ERCF Carrot on a Stick v2.step
98.6 x 6.05 x 10.9 mm
LEDs
Capacitors
PCB
Connector
Header Comb
Header 1
Header 2

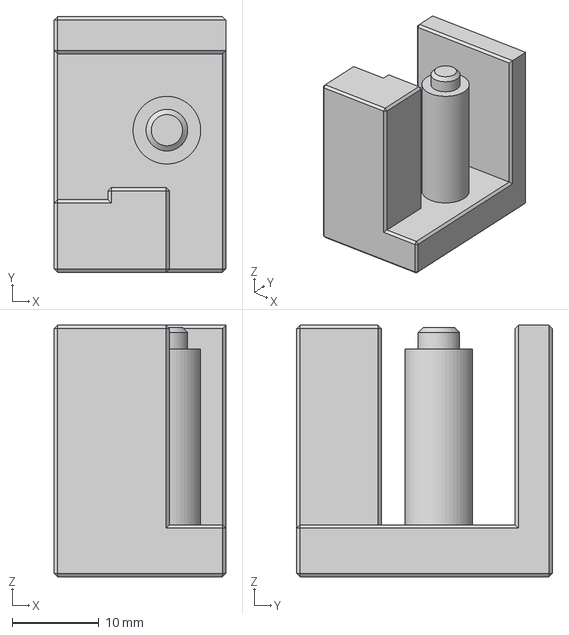
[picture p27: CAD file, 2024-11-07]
CAD/Misc/Filament_Block_Bearing_Insert_Tool.step
19.8 x 29.5 x 29.0 mm

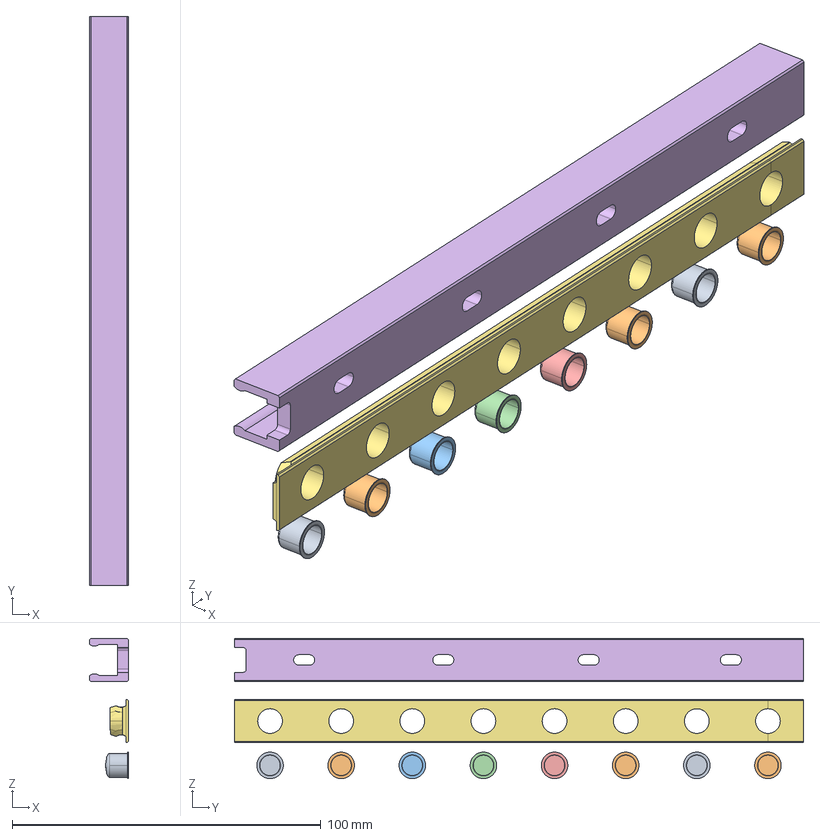
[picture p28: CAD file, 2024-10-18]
Gerber/ERCF LED 8 channel.stp
12.5 x 184.4 x 45.5 mm

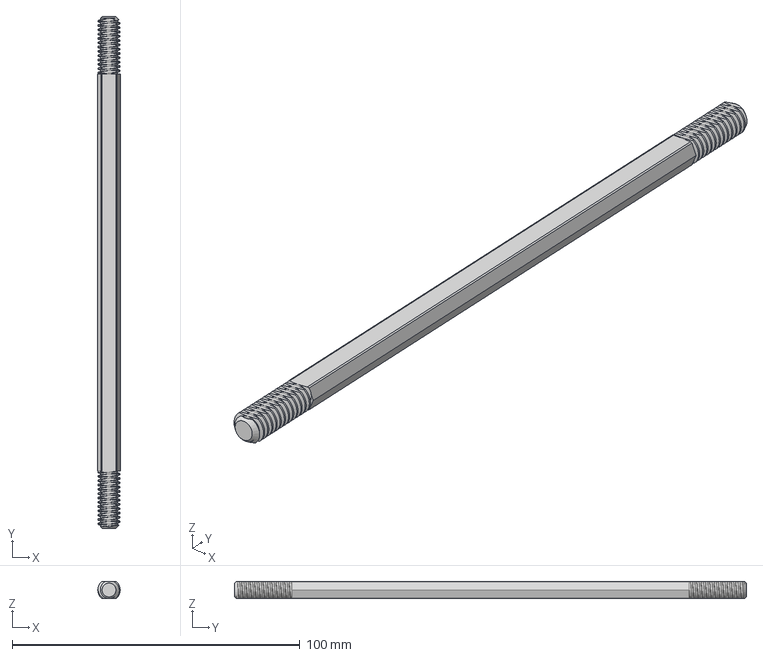
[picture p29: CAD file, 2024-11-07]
Recommended_Options/ERCT_Buffer/CAD/STEP/Axle/Axle_6_Double_Thread.step
7.90 x 178.0 x 5.94 mm

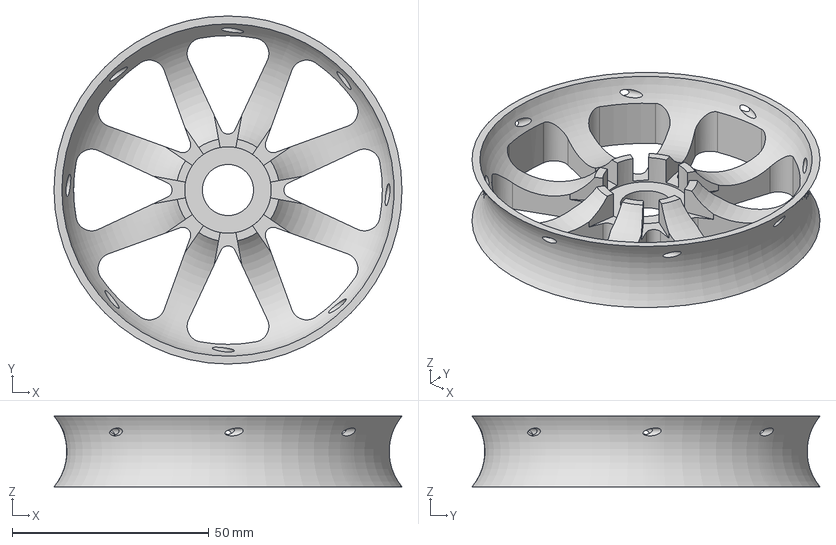
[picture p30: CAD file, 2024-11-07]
Recommended_Options/ERCT_Buffer/CAD/STEP/Buffer_Wheel/Buffer_Wheel_xN.step
88.5 x 88.5 x 17.9 mm

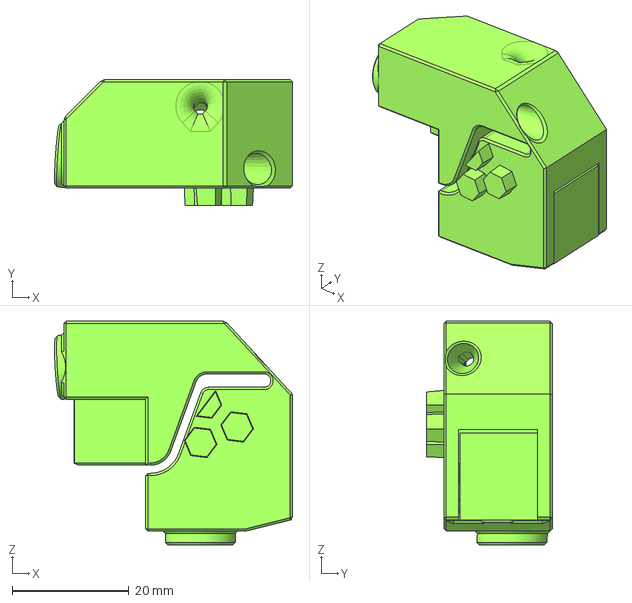
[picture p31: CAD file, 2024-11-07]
Recommended_Options/ERCT_Buffer/CAD/STEP/Coupler_Block/Coupler_Block_MMB_v3_Microswitch.step
40.8 x 21.6 x 38.3 mm

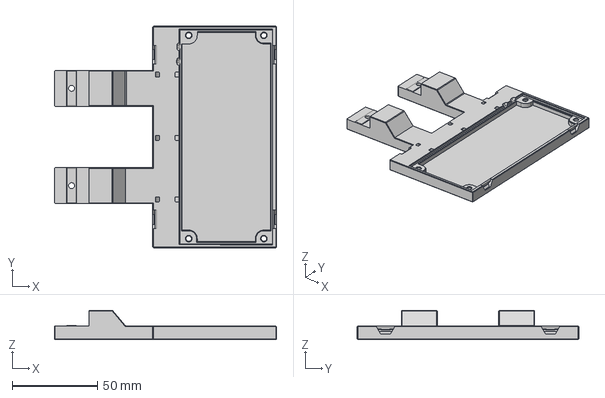
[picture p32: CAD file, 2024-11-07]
Recommended_Options/ERCT_Buffer/CAD/STEP/MMB_Rear_Mount/[a]BTT_MMB_rear_mount.step
130.0 x 129.8 x 17.2 mm

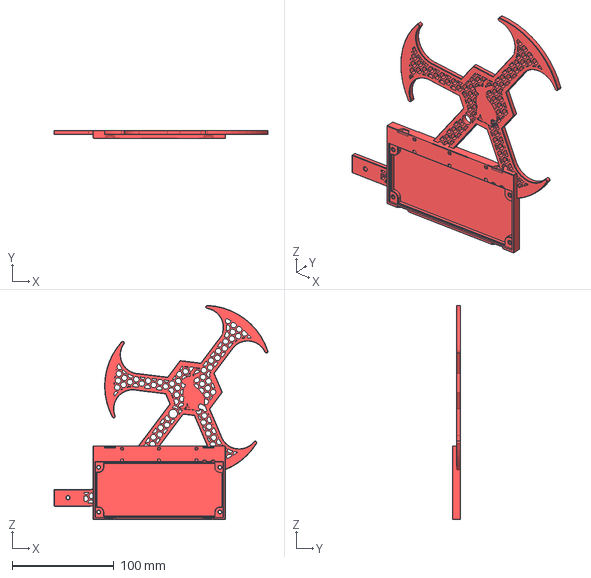
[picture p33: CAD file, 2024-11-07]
Recommended_Options/ERCT_Buffer/CAD/STEP/Support_Arms/[a]_Support_Arm_Endcap_With_MMB.step
210.1 x 8.05 x 210.4 mm

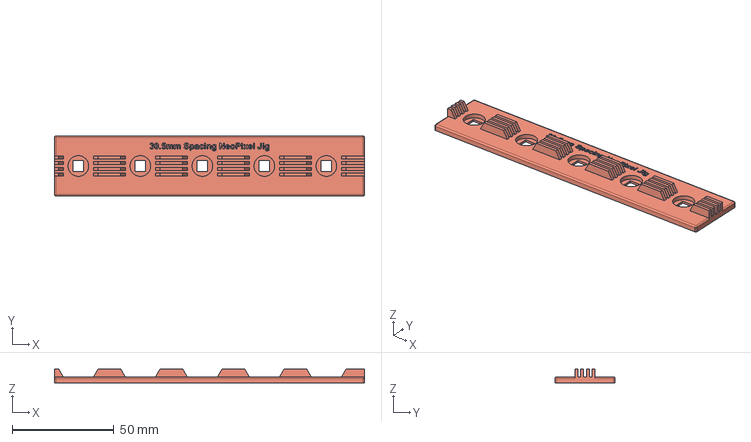
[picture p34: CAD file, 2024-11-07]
Recommended_Options/ERCT_Buffer/CAD/STEP/Tools/LED_Soldering_Tool.step
152.5 x 29.5 x 7.00 mm

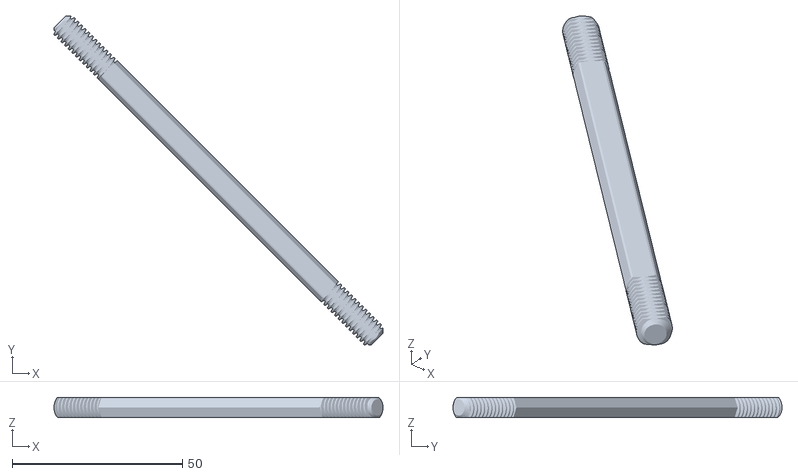
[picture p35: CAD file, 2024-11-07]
Recommended_Options/ERCT_Buffer/CAD/STL_V.3/Axle/Axle_4_Double_Thread.stl
96.7 x 96.7 x 5.94

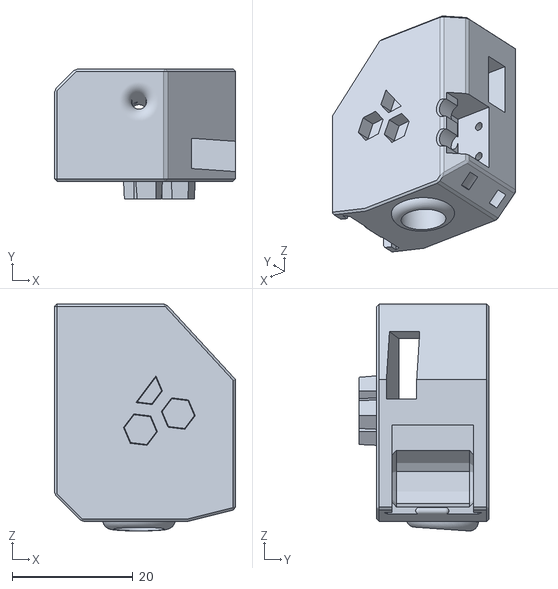
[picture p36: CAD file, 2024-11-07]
Recommended_Options/ERCT_Buffer/CAD/STL_V.3/Coupler Block/coupler_block_xN.stl
30.0 x 21.5 x 37.6

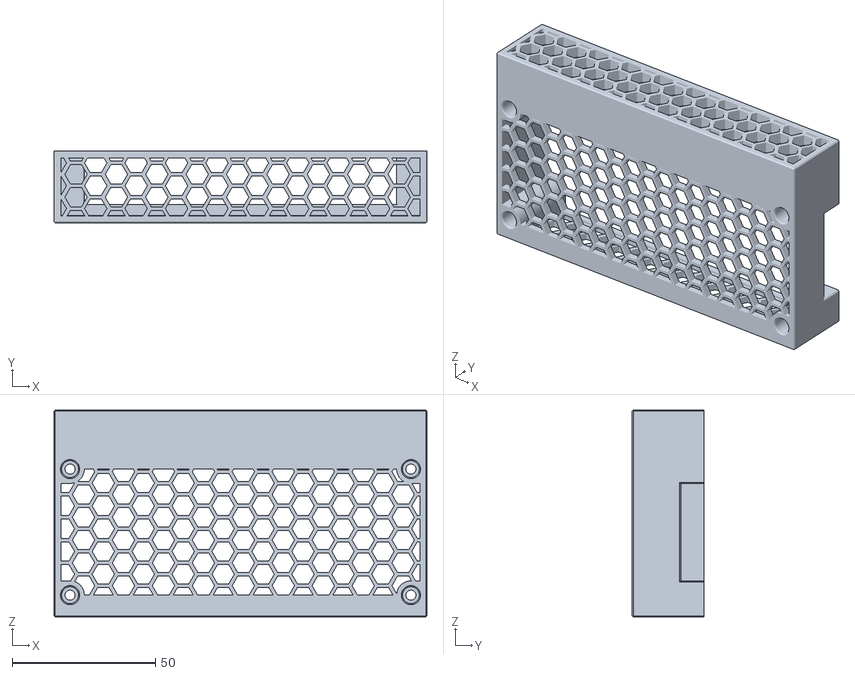
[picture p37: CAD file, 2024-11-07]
Recommended_Options/ERCT_Buffer/CAD/STL_V.3/Support_Arm/[a]BTT_MMB_case_top.stl
130.2 x 25.0 x 72.2

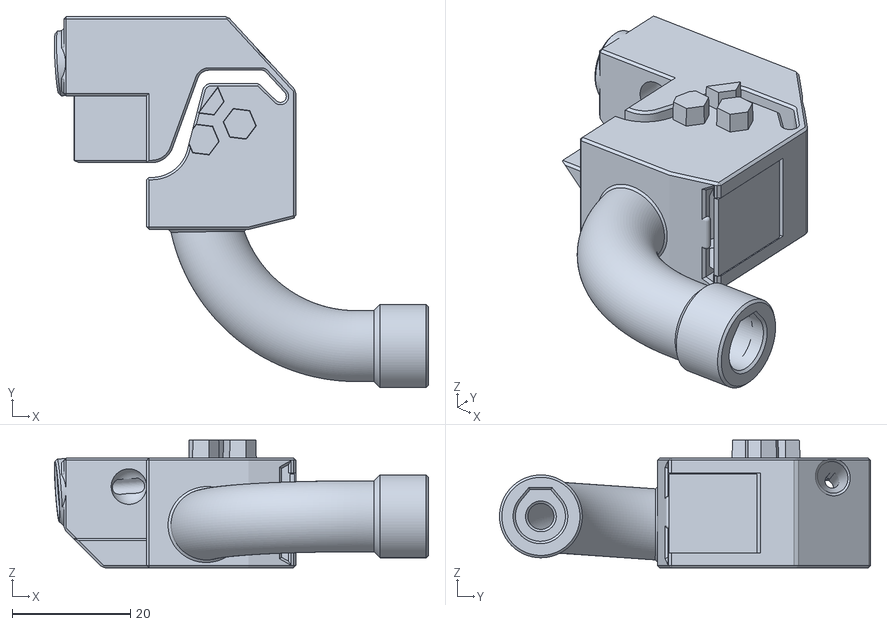
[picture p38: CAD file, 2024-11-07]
Recommended_Options/ERCT_Buffer/Options/180_Degree_Build/Coupler_Block/[a]_Coupler_Block_180_xN.stl
63.2 x 62.7 x 21.6

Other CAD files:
Recommended_Options/ERCT_Buffer/Options/180_Degree_Build/Support_Arms/[a]_Magnetic_PTEF_Coupler_B.stl
Recommended_Options/ERCT_Buffer/Stls/Axle/Axle_10_Double_Thread.stl
Recommended_Options/ERCT_Buffer/Stls/Coupler_Block/[a]_LED_Carrier_xN.stl
Recommended_Options/ERCT_Buffer/Stls/Support_Arm/[a]_Support_Arm_Endcap_No_Electronic_Box.stl
CAD/Misc/Apron_Neopixels/ERCF Carrot on a Stick v2.f3d
CAD/Misc/Apron_Neopixels/LED_Soldering_Tool.f3d
CAD/Misc/Apron_Neopixels/LED_Soldering_Tool_24mm.f3d
CAD/Misc/Apron_Neopixels/Neopixel_Apron_Led_Holder.step
CAD/Misc/Apron_Neopixels/Neopixel_apron_PCB_Led_Holder.step
CAD/Misc/Calib_Test_redux.step
CAD/Misc/Encoder_v23.step
CAD/Misc/Filament_Block_Bearing_Insert_Tool.f3d
CAD/Misc/Gear_Box_Front_With_LED.step
CAD/Misc/NEMA17_Tool_v2.step
CAD/Misc/PTFE_Tool.f3d
CAD/Misc/[a]_ERCF_Easy_Brd_Bracket_Bottom_Mount_With_Cable_Path.step
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

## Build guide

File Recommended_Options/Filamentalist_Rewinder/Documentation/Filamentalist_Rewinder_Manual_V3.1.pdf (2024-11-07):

# ERCF

### Video Assembly Guide Here! (https://youtu.be/5Qk3N2sKz40)

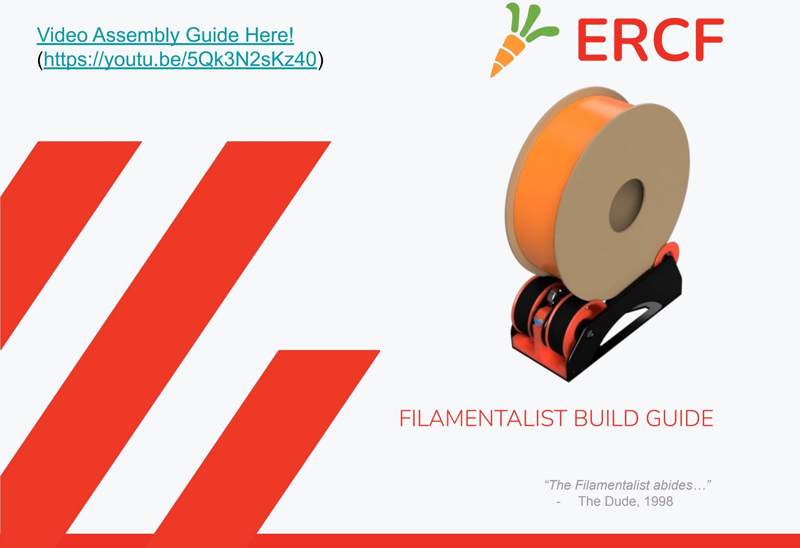
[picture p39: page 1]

# FILAMENTALIST BUILD GUIDE

“The Filamentalist abides…”
- The Dude, 1998

### (https://youtu.be/5Qk3N2sKz40)

ENRAGED RABBIT CARROT FEEDER (ERCF)

Enraged Rabbit Filamentalist Rewinder CAD version: V3

2 | 2

FILAMENTALIST

Introduction
Theory of Operation | 3
Acknowledgements | 4
Configuration/Options | 5
Part Printing Guidelines | 7
STL File Naming Key | 9
Hardware Reference | 10
Required Tools | 11
CAD Files and Parametric Model | 14

## TABLE OF CONTENTS

Assembly | 18
Drive Roller | 19
Idler Roller | 22
Tensioner Mount | 24
Base | 29
Tuning | 35
O-Ring Replacement | 36

Be Kind Rewind
–2008 starring Jack Black and Mos Def

ENRAGED RABBIT CARROT FEEDER (ERCF)

### INTRODUCTION

The Filamentalist is an integrated solution for buffering and spool holding, providing space savings as well as the potential for filament path reduction, and the associated drag/resistance that comes with long runs from spool to buffer to MMU.
- The Filamentalist uses the axial force delivered by the MMU gear motor along the filament to load and unload to and from the filament spool.
- An adjustable spring clamp forces the filament against two o-rings that sit on the drive pulley to create a high traction interface, for rotating the axle and filament spool.
- A one-way clutch style bearing locks against the drive shaft and rotates the filament spool, to take up filament during an unload.
- For loading and print extruding, the clutch disengages allowing for effective free-spooling of the filament spool similar to a roller style spool holder.
- The difference in diameter of the filament driven clutched roller versus the larger roller that the filament spool sits on provides the needed gear ratio to produce enough rotations to take up, and unload a nearly empty or full filament roll.
- During unloading/buffering, to account for the varying diameter of a spool from full to empty filament tension will cause the spring loaded arm to lift a small amount and release traction from the o-rings allowing slip to occur between the filament and the o-ring interface of the rewinder (full spool = max slip, empty spool = no/minimal slip).

THEORY OF OPERATION

ONE-WAY BEARING

O-RING/FILAMENT
INTERFACE

GEAR RATIO FOR
EMPTY-TO-FULL
SPOOL RANGE

ENRAGED RABBIT CARROT FEEDER (ERCF)

### INTRODUCTION

I would like to acknowledgement and thank:
Thisiscam who shared Muzi Xiaoyang's video of a filament driven rewinder and then continued to partner and share his brilliance in the evolution and optimization of the final product.

The Beta Test Team who provided design validation and innumerous inputs for design improvements, printability, and simplification of assembly.
Cheesefrog
Grafton
Biokeks
Meltiseugen
and many more…

All the Early Adopters who allowed a fleet of hundreds of rewinders to help further refine the Filamentalist, the documentation, and volume unit validation. You know who you are!
The ERCF Team for building, supporting, and allowing me to be part of this amazing ecosystem of multi-material printing solutions! Your creativity, commitment, professionalism, collaboration, generosity, and sense of community is an inspiration!

ACKNOWLEDGEMENTS

ENRAGED RABBIT CARROT FEEDER (ERCF)

Things that you need to know include:

There are multiple options for the Filamentalist. Determine which versions/options you want and select the stl's to print accordingly.

- Unit Width: 80mm, 100mm, and custom width via Fusion 360 parametric model
- Mounting Style: Standard (shelf) mount, 2020 rail clip-in mount, 2020 clip-in mount for Filamentalist Enclosure

Based on your mounting needs, you may or may not need to print and install the Base Plate part. It is really only needed if you don't plan to attach the rewinder to a surface.

Feed Direction: The orientation of your MMU with respect to your filament spools location may require a front, rear, or bottom loading capability from the rewinder. Tensioner Mount options are provided to support this.

Pre-gate Sensors: If your MMU does not have pre-gate sensors, and the software you use supports them (like Happy Hare), there are CottonTail pre-gate sensors and Filamentalist Tensioner Mount options that support this.

If you are using, or upgrading from an ERCFv1 or v2 RC1A version you may want/need a higher torque gear motor. Many in the Beta team ran NEMA 17's spec'd at 55 N-cm max torque and config'd them for 1-1.5A (probably overkill...). Grafton's 40 Tooth NEMA 17 Mod (https://www.printables.com/model/692720-ercf-40-tooth-gear-modifiction) is a good addition for gaining more speed from a high torque motor. This may not be required, so if you already have built your ERCF, try the Filamentalist with the motor/gearing you have and decide if you need more torque/speed.

INTRODUCTION

CONFIGURATION/OPTIONS CONSIDERATIONS

ENRAGED RABBIT CARROT FEEDER (ERCF)

The “standard” Filamentalist has an 80mm axle and supports a maximum spool width of 68mm and supports most standard 1, 0.5, and 0.25KG spool sizes and still be able to fit 6 rewinders across the top of a 350 size Voron printer. Some spools such as NinjaFlex and KVP's are too wide to fit the 80mm design. If you use spools wider than 68mm there is also step and stl files posted for a 100mm axle length version. If you are using Autodesk Fusion 360, the provided .f3d file in the CAD directory is a parametric based model allowing you to customize the width of your rewinder to suit your max/min spool widths and/or to design around a standard available steel axle length (see Parametric CAD Model section in this document).

Because the standard tuning of this design relies on some filament slip at the o-rings, the o-rings may ultimately wear-out. Testing and extrapolation estimates that the wear-out point is ~5K cycles. See the O-Ring Replacement section at the end of this document for o-ring swap/replacement instructions.

Questions or input?

Refer to the:

Filamentalist FAQ (https://github.com/Enraged-Rabbit-Community/ERCF_v2/blob/master/Recommended_Options/Filamentalist_Rewinder/Filamentalist_FAQ.md)

Troubleshooting Guide (https://github.com/Enraged-Rabbit-Community/ERCF_v2/blob/master/Recommended_Options/Filamentalist_Rewinder/troubleshoot.md)

Filamentalist Discord Channel (https://discord.gg/uDcGxukRKd)

Enjoy the process of building as much as utilizing your Enraged Rabbit Carrot Feeder (ERCF) and Filamentalist Rewinder!

INTRODUCTION

CONFIGURATION/OPTIONS CONSIDERATIONS (continued)

ENRAGED RABBIT CARROT FEEDER (ERCF)

The ERCF team has provided the following print guidelines. We recommend you to follow them in order to have the best chance at success with your parts. There are often questions about substituting materials or changing printing standards, but we recommend you follow these.

The majority of mechanical issues users experience with the ERCF and its supporting components can be traced back to print quality and and accuracy. Please take the time to print the calibration tools and dial in your printer before moving forward.

INTRODUCTION

FDM MATERIAL
The Filamentalist was designed for, and
tested with ABS and ASA. Based on the tolerance requirements of the design we recommend to only use ABS OR ASA.

INFILL TYPE
Grid, Gyroid, Honeycomb, Triangle or Cubic.

LAYER HEIGHT
Recommended : 0.2mm
First Layer: 0.25mm

INFILL PERCENTAGE
Recommended: 40%

EXTRUSION WIDTH
Recommended : Forced 0.4mm

WALL COUNT
Recommended : 4

SOLID TOP/BOTTOM LAYERS
Recommended : 5

### PART PRINTING GUIDELINES

ENRAGED RABBIT CARROT FEEDER (ERCF)

IMPORTANT !! The Filamentalist design relies on multiple press-fits for bearings and ECAS fittings. As a result, printer calibration is important. A Test_Block stl is included. It is highly recommended that you print this block first, check fits, and make adjustments to extrusion multipliers and/or slicer scaling if needed before printing the Filamentalist parts.

INTRODUCTION

### THE TEST BLOCK CALIBRATION TOOL

Test_Block.stl

M3 Thread Cutting Hole

ECAS Hole

608 Bearing Hole

TESTS
Insert the different pieces of hardware in their dedicated positions: ECAS fitting, M3 screw thread in, and 608 bearing.

The ECAS fitting should be a tight, snap-in fit. If the plastic cracks after ECAS insertion due to too tight a fit or the ECAS is a loose fit then extrusion rates and/or interior hole settings need to be adjusted in your slicer. You may need to cut the print with clippers to remove the ECAS.

You should be able to hand press in a 608 bearing into the pocket. It is acceptable if additional force, like light hammer taps is required to fully seat the bearing. The bearing can be removed by inserting an 8mm axle/rod through the bearing and rocking the rod back and forth while gently pulling on the rod, “walking” the bearing out of the pocket.

Screw an M3 screw into the back side (opposite ECAS hole). The screw should tightly screw in and cut threads into the plastic. If the ECAS and 608 bearing press in nicely but this hole is tight, no print adjustments need to be made but M3 screw holes may need to be opened up hand turning a 2.5mm drill bit.

ECAS

608 Bearing

ENRAGED RABBIT CARROT FEEDER (ERCF)

FILE NAMING
By this time you should have already downloaded our STL files from the ERCF GitHub. This is how to use the naming conventions.

Part_Name]_[Width_Version]_[Quantity_Required]_[option].stl

Example [a]_Rim_Roller_80mm_x2.stl

INTRODUCTION

PRIMARY COLOR
Example Left_Support.stl
These files will have nothing at the start of the filename.

ACCENT COLOR
Example
[a]_Center_Drive_Roller.stl These files have an ‘’[a]_’’ prefix to denote that they should be printed with an
accent color.

WIDTH VERSION
Filenames with an ‘’80mm’’ or “100mm” after the file
name are specific to the
width option you choose to build.

QUANTITY REQUIRED
Filenames ending with ‘’_x#’’ are telling you the quantity of that part required to build a single rewinder

STL FILE NAMING KEY

[option]
Filenames with an ‘“[option]”after the filename or width are build options/alternatives such as:
- Clip-In style mount
- Supports for the Filamentalist Enclosure
- Pre-gate sensors included in Tensioner Mounts

ENRAGED RABBIT CARROT FEEDER (ERCF)

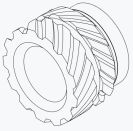
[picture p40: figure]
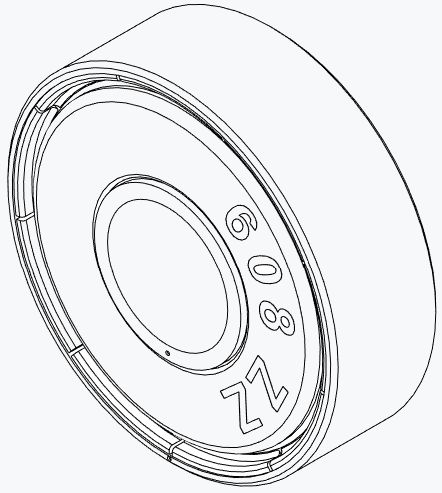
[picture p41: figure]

10 | 10

INTRODUCTION

FLAT HEAD COUNTERSUNK SCREW (FHCS)
Metric fastener with a cone shaped head and a flat top.

ISO 10642

SOCKET HEAD CAP SCREW (SHCS) Metric fastener with a cylindrical head and hex drive. The most common fastener used on the ERCF.

ISO 4762

WASHER
Plain metal stamped washer.

DIN 125

SELF TAPPING SCREW
Fastener with a pronounced thread profile that is screwed directly into plastic. Used with optional pre-gate sensor Filamentalist version.

HEAT SET INSERT
Brass, threaded, with ridges on the outside. Heat to approx 250C with soldering iron and push into a hole in the plastic. Plastic cools and solidifies around the knurls/ridges for excellent resistance to torque and pull-out.

608 BEARING
For the Filamentalist, the 2RS (sealed) style is preferred but can be used with the open or ZZ (shielded) style.

ECAS FITTING
4mm Push -Fit PTFE tubing fitting.

SPRING
For the Filamentalist, 304 Stainless Steel,6mm OD, 0.6-1mm Wire Size, 15mm Free Length spring used in Tensioner Assembly.

HARDWARE REFERENCE

ENRAGED RABBIT CARROT FEEDER (ERCF)

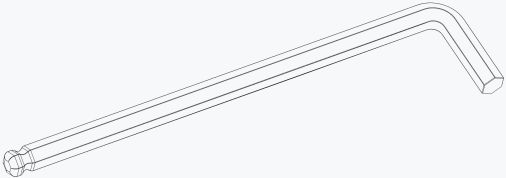
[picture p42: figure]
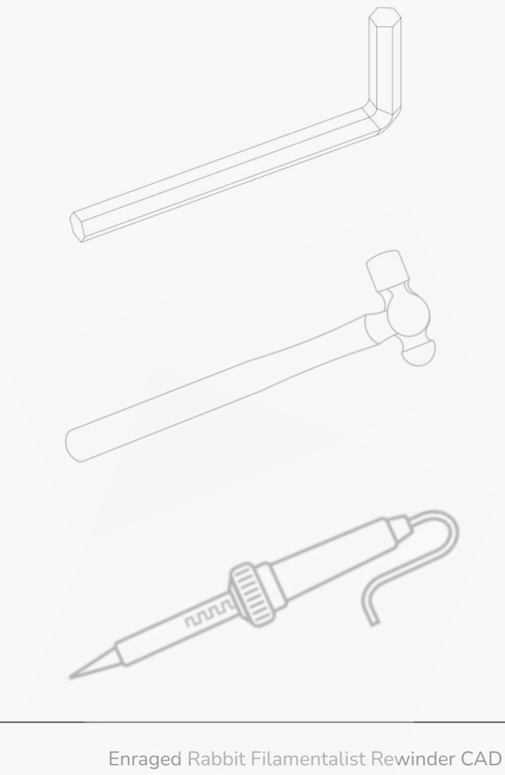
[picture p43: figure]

11 | 11

INTRODUCTION

BALL-END HEX DRIVER
Adjustment of the Tensioner screw in this design benefits from the use of a 2.5mm ball-end hex driver.

2MM HEX DRIVER
The 2mm hex driver will see a lot of use in this build. A quality driver is strongly recommended. Refer to the sourcing guide for suggestions.

SOLDERING IRON
For the insertion of the single heat set insert in the Tensioner Mount part of the Filamentalist rewinder

SMALL HAMMER
A small hammer my be useful/required to tap in press-fit bearings.

TOOLS

ENRAGED RABBIT CARROT FEEDER (ERCF)

12 | 12
INTRODUCTION | TOOLS

ANGLE GRINDER/DREMEL
For cutting 8mm axle rods/tubes to length if
required.
VISE
A vise is handy cutting 8mm axles.
CAD SOFTWARE
Filamentalist_80mm/100mm.step or Filamentalist_(parametric).f3d
Software is a tool too! The CAD file for the Filamentalist was designed to be used along with this manual as a supplement or reference, even if you aren’t a CAD Pro. You can use the free edition of Fusion360, or your choice of CAD program such as TinkerCAD, onshape, or FreeCAD.
SUPERGLUE
Yes, we consider this a tool. Superglue may be useful if your print tolerances result in slip-fits for the bearings and ECAS. Cheap, single-use gel tubes are fine.

TEST BLOCK TOOL
ERCFv2/Recommended_Options/Filamentalist_Re winder/Stls/Test_Block.stl
It is highly recommended that you print this Test_Block.stl part first, check fits of M3 screws, 608 bearings, and the ECAS fitting, and make adjustments to extrusion multipliers and/or slicer scaling if needed before printing the Filamentalist parts.
AXLE DEPTH TOOL
ERCFv2/Recommended_Options/Filamentalist_Re winder/Stls/##mm_Axle/Axle_Depth_Tool.stl Helps you set the depth that the Rim Roller parts are attached on the axle to ensure free floating CDR Spacer parts and the correct overall width of the rewinder.

ENRAGED RABBIT CARROT FEEDER (ERCF)

If you need assistance with your build you can head over the Filamentalist Discord group and post your questions in the ercf_questions channel. It is the primary medium to help people with their ERCF build and tuning! You can also check the Github page for the latest releases.

INTRODUCTION

### Discord Link (https://discord.gg/uDcGxukRKd)

GitHub Link (https://github.com/Enraged-Rabbit-Community/ERCF_v2/tree/master/Recommended_Options/Filamentalist_Rewinder)

HOW TO GET HELP

ENRAGED RABBIT CARROT FEEDER (ERCF)

We have provided the Filamentalist CAD files (ERCFv2/Recommended_Options/Filamentalist_Rewinder/CAD/Filamentalist_##mm.step and Filamentalist_(parametric).f3d), so that you can follow along with the instructions in a 3D view, if you like.

The CAD file is organized into folders based on the instructions in this manual. First hide all the parts, and then reveal the parts up to the step you are on in this manual, and the CAD should match what you are building.

All of the non-printed parts are in each section’s Hardware folder.

INTRODUCTION

USING THE CAD FILES

ENRAGED RABBIT CARROT FEEDER (ERCF)

If you are using Autodesk Fusion 360 the “Filamentalist_(parametric).f3d file provided in the CAD folder is a parametric based model allowing you to customize the width of your rewinder to suit your max/min spool widths and/or to design around a standard available steel axle length. The model will update and accurately show the results of these parameters to help you visualize the acceptability of the result as well as provide reference dimensions to aid in part sourcing.
To customize your Filamentalist width and axle sizing, load the model, make sure you are in the "Solid" menu, and then select "Modify" and "Change Parameters"

INTRODUCTION

THE PARAMETRIC CAD MODEL

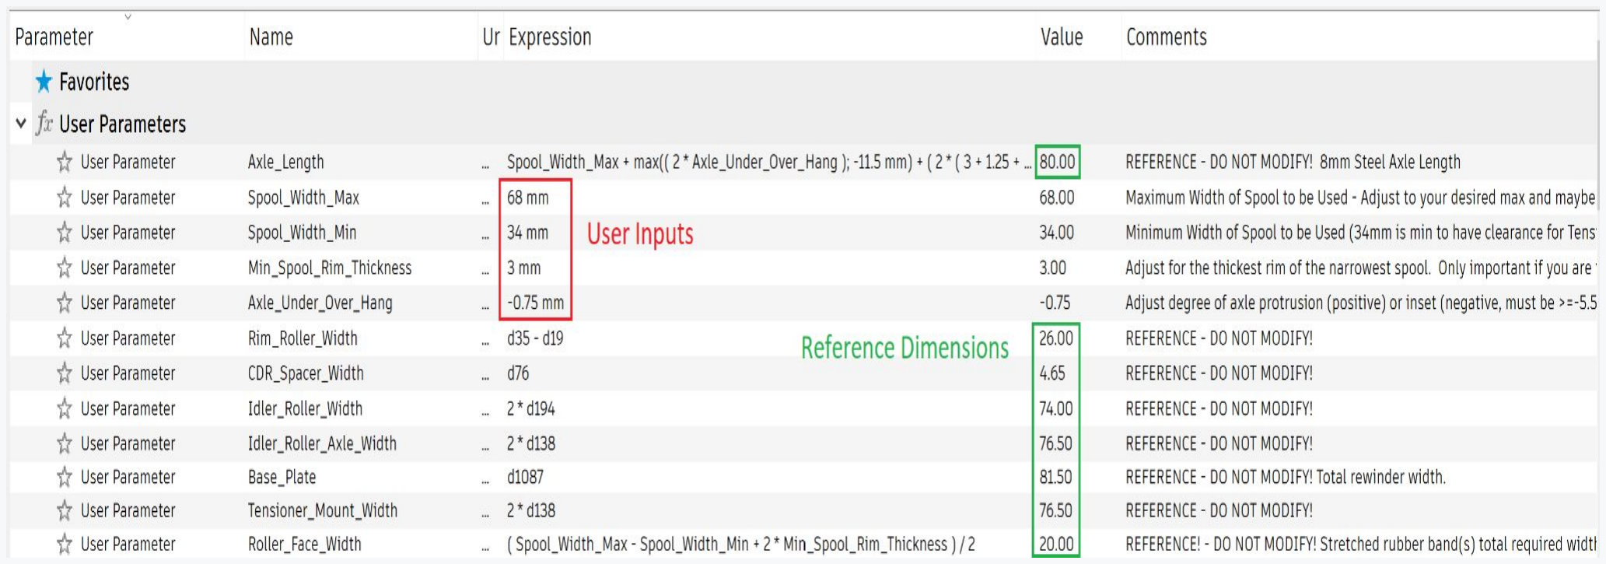
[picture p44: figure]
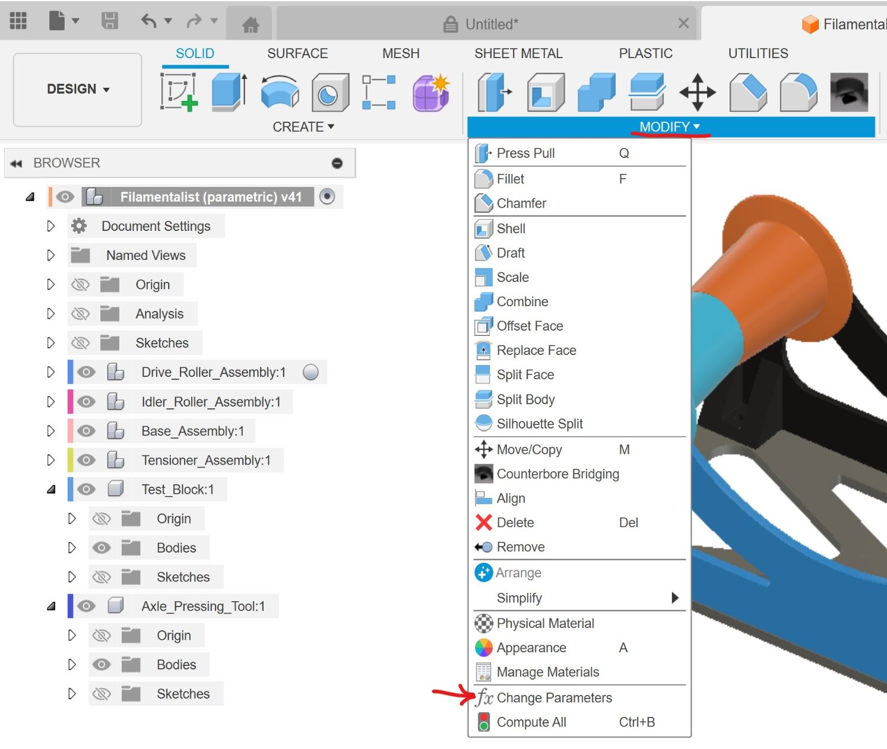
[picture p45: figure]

Adjust the following parameters to meet your needs:
Spool_Width_Max - Set this to accommodate the widest filament spool you expect to use. It is recommended to add ~2mm to this number to allow for spool width and rim straightness/variation.

(parameter descriptions continued on next page)

ENRAGED RABBIT CARROT FEEDER (ERCF)

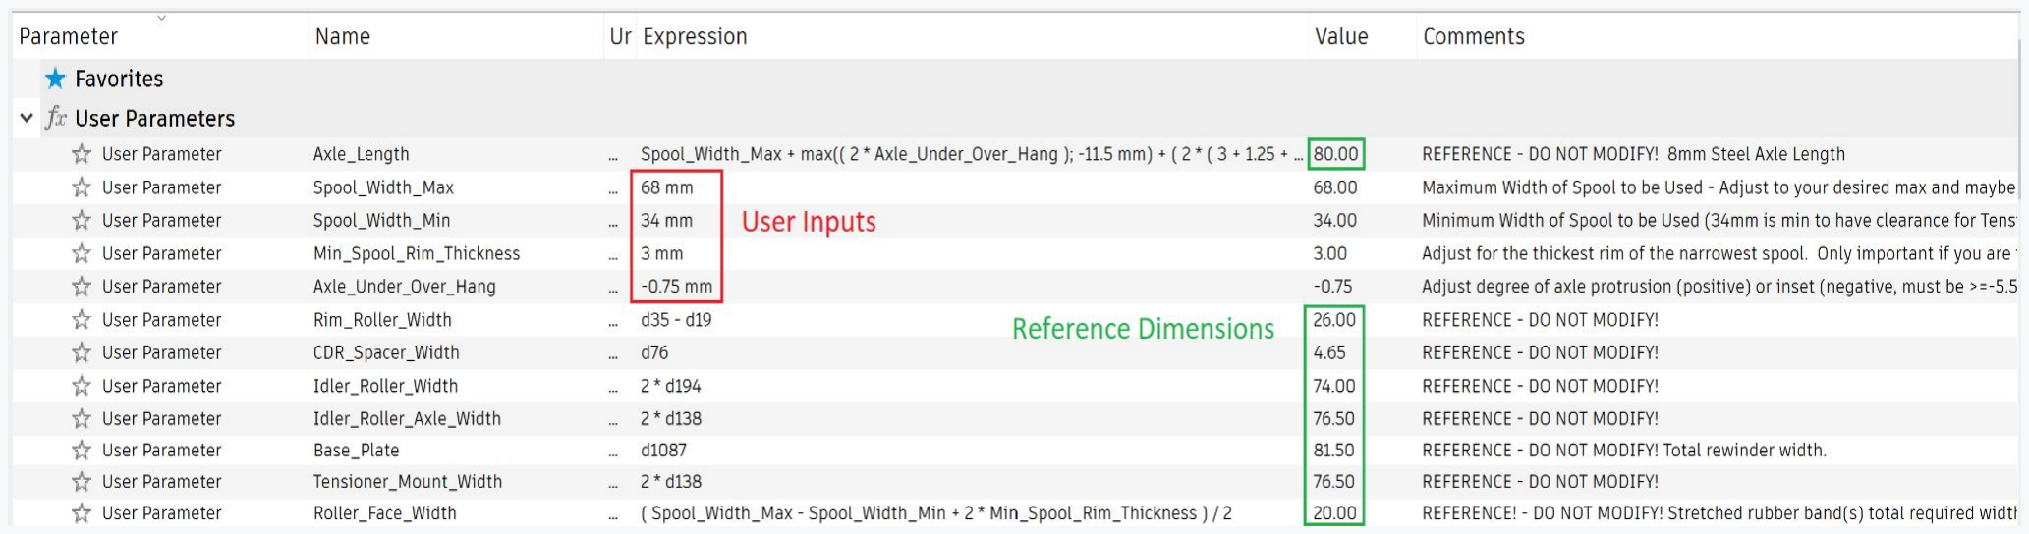
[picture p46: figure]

16 | 16

INTRODUCTION

THE PARAMETRIC CAD MODEL (continued)

Adjust the following parameters to meet your needs (continued from previous page):
Spool_Width_Min - Set this to accommodate the narrowest filament spool you expect to use. Due to the width of the Tensioner Assembly the minimum spool width is constrained at 34mm and will default to this number if you enter something less than 34mm. If you don't expect to use narrow spools (like 250kg or 500kg spools) you can set this to a larger number to produce narrower Rim Rollers. Narrower Rim Rollers will reduce print time and filament consumed and may allow for usage of more standard, less expensive, and/or fewer rubber bands but will limit overall future flexibility of your rewinder.

Min_Spool_Rim_Thickness - Normally this can be left at the default of 3mm but if you are trying to squeeze narrow spools onto the rewinder, you are close to that 34mm minimum width, and your narrow spool rims are less than 3mm thick, you can adjust for your thickest rim of your narrowest spool to make it fit the rewinder.

ENRAGED RABBIT CARROT FEEDER (ERCF)

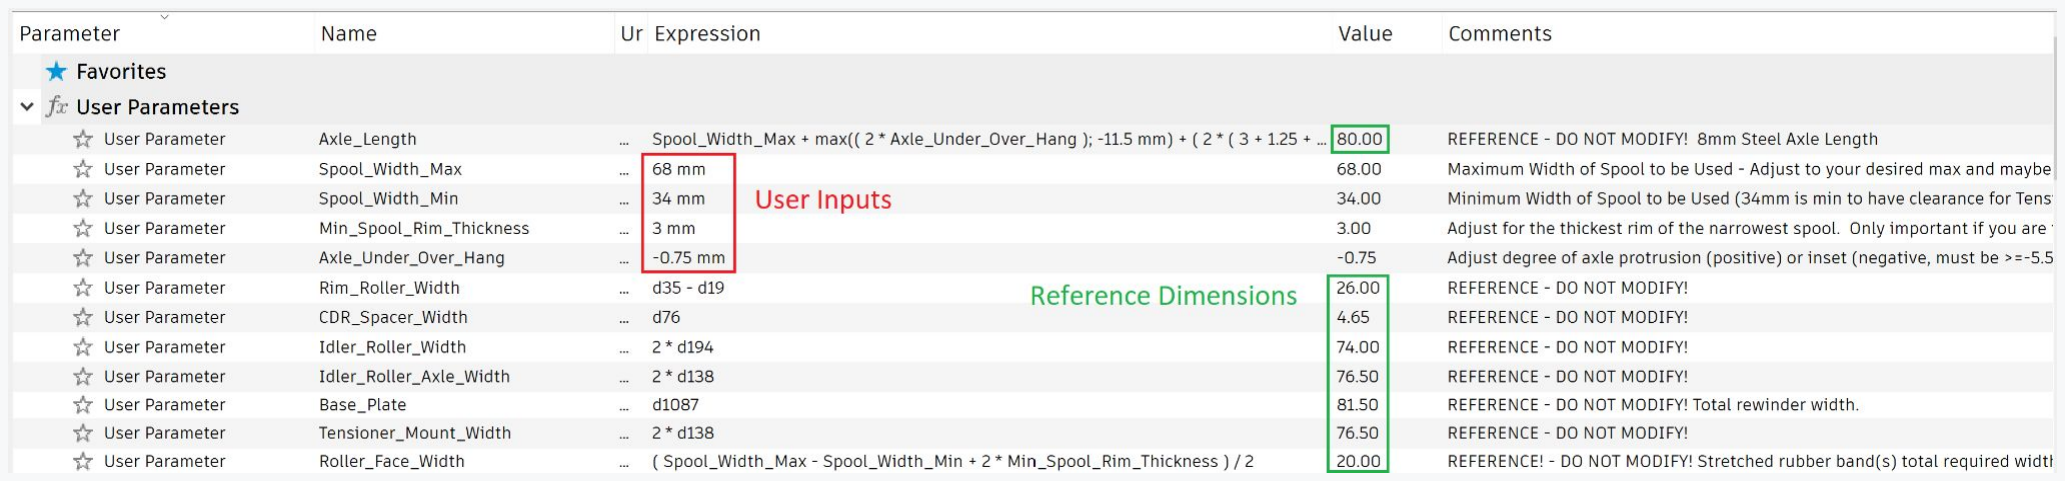
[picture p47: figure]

17 | 17

INTRODUCTION

THE PARAMETRIC CAD MODEL (continued)

Adjust the following parameters to meet your needs (continued from previous page):
Axle_Under_Over_Hang - This can be either a positive or negative number and is used to tweak the design to use a standard available axle length (like 80mm or 100mm). A negative number will result in the axle ends sitting inside the footprint of the rewinder but the model logic will not let you underhang more than 5.5mm inside the 608 bearing race to ensure good support of the axles from the bearings. A positive number will result in the axle protruding beyond the footprint of the rewinder. You may want to do this if you are going to use a readily available 100mm length axle but don't need a rewinder that can support spool widths as wide as 86mm, thus saving printing time and plastic by using a lesser Spool_Width_Max like 75mm. The best case scenario is to set this value at 0 and you have the ability to cut shaft stock to the exact length for your desired Spool_Width_Max (i.e. Spool_Width_Max = 75mm to accommodate virtually all 1KG spools and cut shaft to 88.5mm length).

Reference Parameters. DO NOT CHANGE THESE! These are included to assess the results of your inputs. You can iterate with changes to the User inputs to arrive at desired max spool width, standard axle widths, and/or readily available rubber band sizes.

The model will update to show the results of these parameters to help you visualize the acceptability of the result.

### OVERVIEW

## Idler Roller Assembly

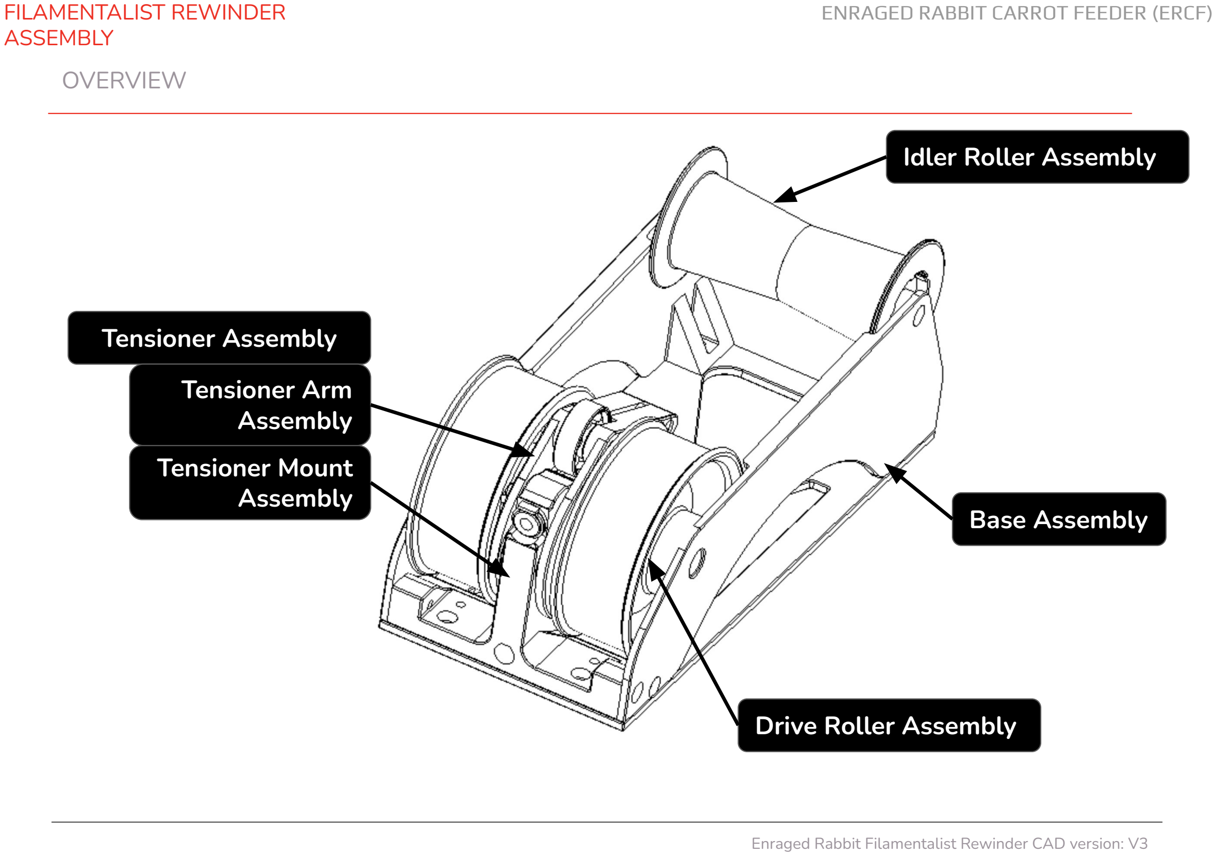
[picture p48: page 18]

ENRAGED RABBIT CARROT FEEDER (ERCF)

FILAMENTALIST REWINDER
ASSEMBLY

## Drive Roller Assembly

## Tensioner Assembly

## Base Assembly

## Tensioner Arm Assembly Tensioner Mount Assembly

ENRAGED RABBIT CARROT FEEDER (ERCF)

### DRIVE ROLLER ASSEMBLY

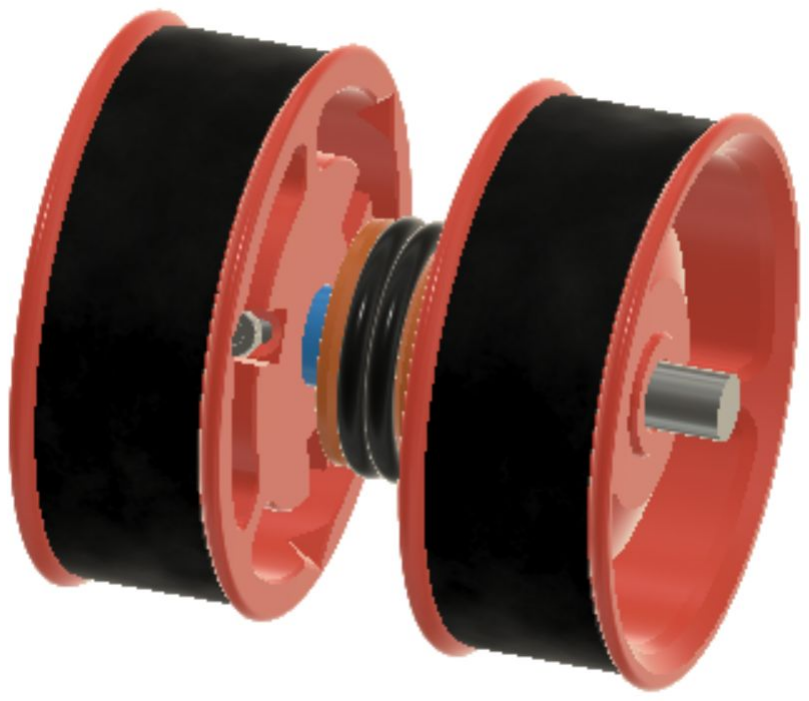
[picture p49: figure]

“You can’t have everything….where would you put it?” –Steven Wright

ENRAGED RABBIT CARROT FEEDER (ERCF)

### DRIVE ROLLER ASSEMBLY EXPLODED VIEW

DRIVE ROLLER ASSEMBLY BOM
(PER CHANNEL)

1x 8x80/100mm Stainless Steel Axle 2x AS568 Standard size 211 O-Ring 1x HF081412 One-Way Bearing 2-6x M3x8 Stainless SHCS Screw 2x Rubber Bands

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
2x [a]_Rim_Roller_80/100mm.stl 1x [a]_Center_Drive_Roller.stl
2x CDR_Spacer.stl
Axle_Depth_Tool.stl

DRIVE ROLLER ASSEMBLY PRINTED PARTS (PER CHANNEL)

A

B

C

F

H

G

D

### ASSEMBLY INSTRUCTIONS

1. Check the resistance of the one-way bearing on the axle. If the resistance is greater than the combined rolling resistance of the rest of the rewinder the one-way bearing will not disengage and freespool properly during filament loads resulting in loose coils on the spool. If you experience this issue please refer to the Filamentalist Troubleshooting Guide. (https://github.com/SkiBikePrint/Filamentalist/blob/main/troubleshoot.md)
2. Stretch O-Rings (part B) onto part G.
3. Press/tap part C into part G. This should be a tight fit. If too loose, use Super Glue or reprint with an increased extrusion factor. If too tight scrape the interior hole of Center Driver Roller with an Xacto knife. Orientation of the one-way bearing does not matter at this point.
4. Install screws into Rim Rollers to cut the threads (using a ball end hex driver makes this easier). Back the screws out a little to allow the axle to be inserted. If center bore of rollers is a close fit, only one screw per roller is required. If a loose fit, use 3 screws per roller to ensure roller is centered on Axle.

I

E

### DRIVE ROLLER ASSEMBLY (continued) EXPLODED VIEW

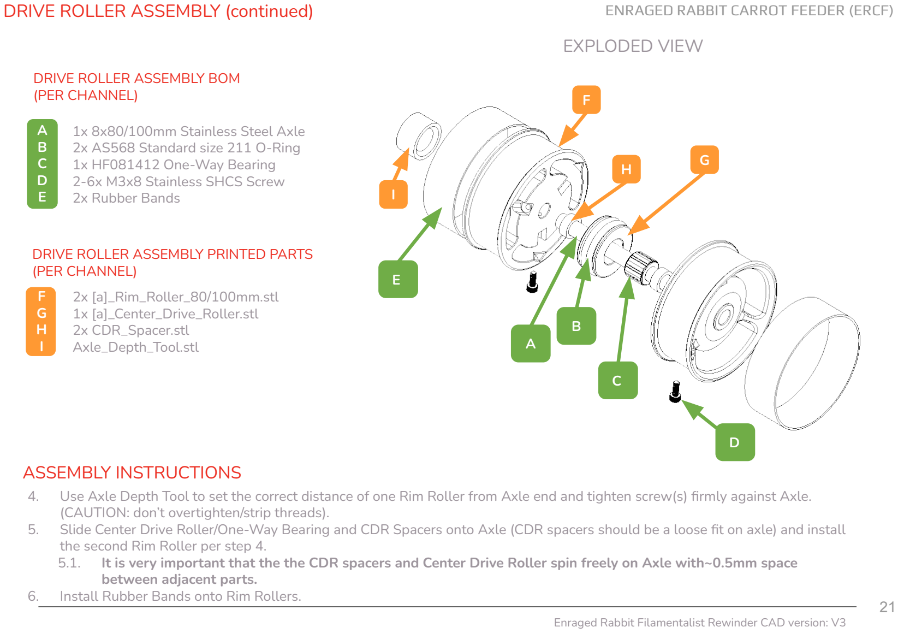
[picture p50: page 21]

ENRAGED RABBIT CARROT FEEDER (ERCF)

DRIVE ROLLER ASSEMBLY BOM
(PER CHANNEL)

1x 8x80/100mm Stainless Steel Axle 2x AS568 Standard size 211 O-Ring 1x HF081412 One-Way Bearing 2-6x M3x8 Stainless SHCS Screw 2x Rubber Bands

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
2x [a]_Rim_Roller_80/100mm.stl 1x [a]_Center_Drive_Roller.stl
2x CDR_Spacer.stl
Axle_Depth_Tool.stl

DRIVE ROLLER ASSEMBLY PRINTED PARTS (PER CHANNEL)

### ASSEMBLY INSTRUCTIONS

4. Use Axle Depth Tool to set the correct distance of one Rim Roller from Axle end and tighten screw(s) firmly against Axle. (CAUTION: don’t overtighten/strip threads).
5. Slide Center Drive Roller/One-Way Bearing and CDR Spacers onto Axle (CDR spacers should be a loose fit on axle) and install the second Rim Roller per step 4.
5.1. It is very important that the the CDR spacers and Center Drive Roller spin freely on Axle with~0.5mm space between adjacent parts.
6. Install Rubber Bands onto Rim Rollers.

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
ENRAGED RABBIT CARROT FEEDER (ERCF)

### IDLER ROLLER ASSEMBLY

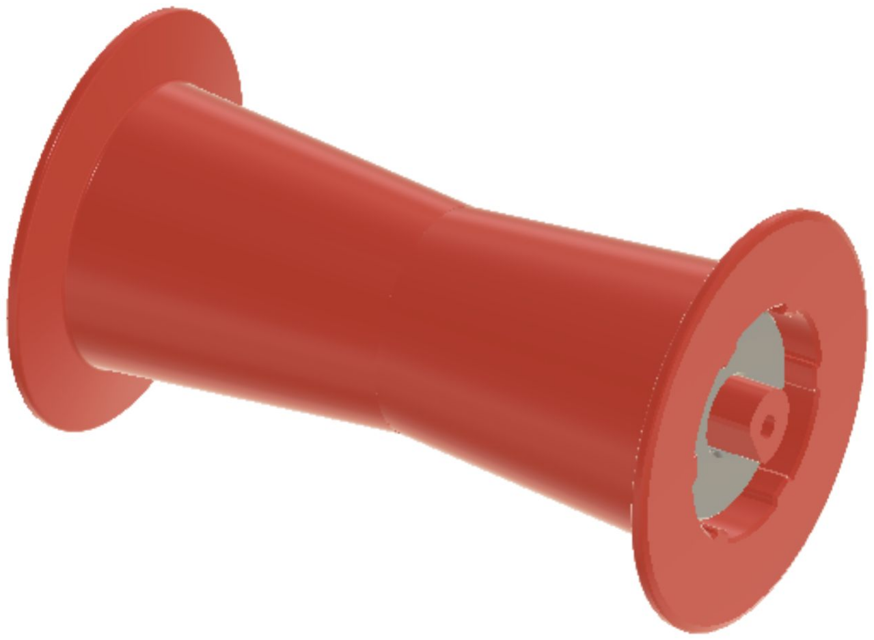
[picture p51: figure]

Q: What do you call a group of rabbits hopping backwards? A: A receding hare line

ENRAGED RABBIT CARROT FEEDER (ERCF)

### IDLER ROLLER ASSEMBLY

### EXPLODED VIEW

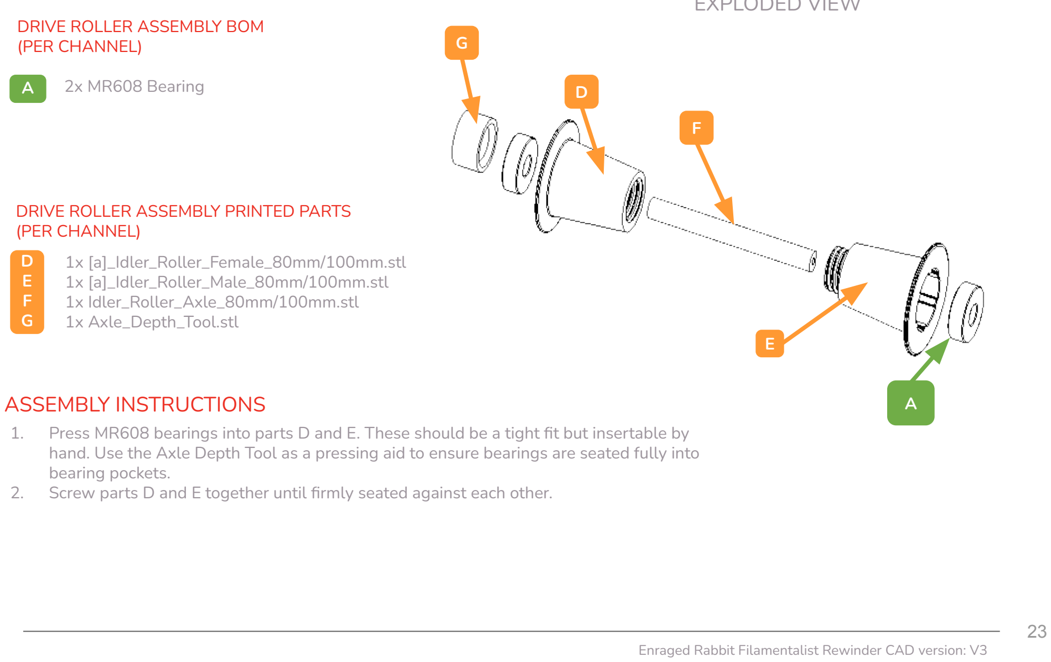
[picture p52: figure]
DRIVE ROLLER ASSEMBLY BOM (PER CHANNEL); A 2x MR608 Bearing; 1x [a]_Idler_Roller_Female_80mm/100mm.stl 1x [a]_Idler_Roller_Male_80mm/100mm.stl 1x Idler_Roller_Axle_80mm/100mm.stl 1x Axle_Depth_Tool.stl; DRIVE ROLLER ASSEMBLY PRINTED PARTS (PER CHANNEL); ASSEMBLY INSTRUCTIONS; bearing pockets.

1. Press MR608 bearings into parts D and E. These should be a tight fit but insertable by hand. Use the Axle Depth Tool as a pressing aid to ensure bearings are seated fully into
2. Screw parts D and E together until firmly seated against each other.

### TENSIONER MOUNT ASSEMBLY

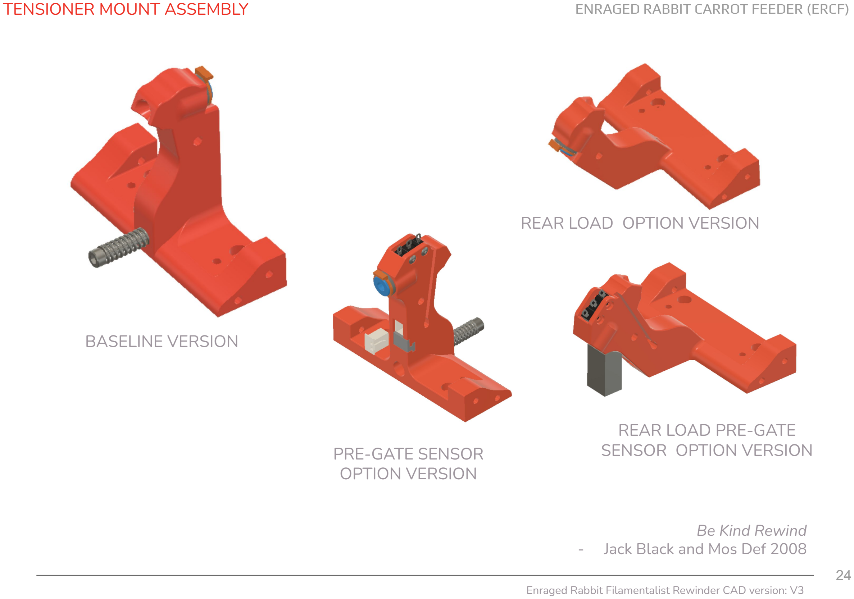
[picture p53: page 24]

ENRAGED RABBIT CARROT FEEDER (ERCF)

### BASELINE VERSION

### PRE-GATE SENSOR OPTION VERSION

### REAR LOAD PRE-GATE SENSOR OPTION VERSION

### REAR LOAD OPTION VERSION

Be Kind Rewind
- Jack Black and Mos Def 2008

ENRAGED RABBIT CARROT FEEDER (ERCF)

### TENSIONER MOUNT ASSEMBLY

TENSIONER MOUNT ASSEMBLY BOM (PER CHANNEL)
ECAS Fitting (remove rubber seal)
3mm Heatset Insert

A
B

F
G

1x [a]_Tensioner_Mount_80mm/100mm.stl
1x [a]_ECAS_Clip.stl (if not on-hand)

TENSIONER MOUNT ASSEMBLY PRINTED PARTS
(PER CHANNEL) | A

F

G

ALTERNATE/OPTIONAL PRINTED PART VERSIONS
(PER CHANNEL)
F 1x [a]_Tensioner_Mount_with_Sensor_80mm/100mm.stl
(split to parts in slicer for print-in-place breakaway connector retaining key) 1x [a]_Tensioner_Mount_Rear_Load_80mm/100mm.stl
1x [a]_Tensioner_Mount_Rear_Load_with_Sensor_80mm/100mm.stl

### EXPLODED VIEW

### ASSEMBLY INSTRUCTIONS

B

1. Install 3mm Heatset Insert.
2. Remove rubber seal and press ECAS Fitting into Tensioner Mount, ensuring it sits flush to face of hole. Using the 8mm axle as a pressing tool can help to get fitting fully inserted. Varying
ECAS and print tolerances could result in the ECAS hole cracking. If this happens, use superglue around the ECAS hole and crack(s).

Built-in
removable
support

PRE-GATE SENSOR
OPTION VERSION

REAR LOAD
OPTION VERSION

REAR LOAD
PRE-GATE SENSOR
OPTION VERSION

ENRAGED RABBIT CARROT FEEDER (ERCF)

### TENSIONER MOUNT ASSEMBLY (SENSOR OPTION)

SENSOR OPTION ADDITIONAL BOM ITEMS (PER CHANNEL)

1x D2F-L3 Microswitch
1x JST-XH 2-pin Socket
2x 60mm 24 AWG wire
2x M2x10 Self-tapping screw

A
B
C
D

F 1x [a]_Tensioner_Mount_with_Sensor_80mm/100mm.stl

TENSIONER MOUNT ASSEMBLY PRINTED PARTS
(PER CHANNEL)

A

B

B

F

ALTERNATE/OPTIONAL PRINTED PART VERSIONS
(PER CHANNEL)
F 1x [a]_Tensioner_Mount_Rear_Load_with_Sensor_80mm/100mm.stl

Built-in removable
support

### EXPLODED VIEW

### ASSEMBLY INSTRUCTIONS

1. Break away print-in-place JST-XH socket retaining clip using small flat blade screwdriver.
2. Install microswitch with 2x M2x10mm self tapping screws.
3. Strip 3mm from 24 AWG wire for JST-XH socket and tin with solder.
4. Feed wire through hole in wire slot and out opening for JST-XH socket.
5. Solder 2x wires at 90 degrees to terminals of JST-XH 2-pin socket and press socket into hole. Slide socket retaining clip back into place.
6. Press wire into slot and wrap around to the two switch terminals denoted with red dots in picture to assess length. Cut wire to length leaving 3mm for stripped ends to solder to terminals.
7. Solder wire to switch terminals.
8. Usa a 2-pin JST-XH plug for a harness running to main or MMU board.

BREAK
AWAY

C

D

ENRAGED RABBIT CARROT FEEDER (ERCF)

### TENSIONER ARM ASSEMBLY

TENSIONER ARM ASSEMBLY BOM (PER CHANNEL)

1x MR608 bearing
3x M3x16/18mm FHCS Screw
1x Spring
1x M3 Washer
1x M3x35mm +/- 10mm SHCS Screw

A
B
C
D
E

C
D

1x Tensioner_Arm_Left.stl
1x Tensioner_Arm_Rightstl

TENSIONER ARM ASSEMBLY PRINTED PARTS (PER CHANNEL)

A

B

C

D

Arm orientation for rear load version

| 1. Remove support from part D.

### EXPLODED VIEW

### ASSEMBLY INSTRUCTIONS

2. Lay part D on a flat surface. Slide the 608 bearing onto the bearing post.
Place part C into the 608 bearing and rotate against the part D making sure the
alignment tab seats correctly into the pocket at the bottom of part C.
3. Place a M3x12/16/18 FHCS screw through the bearing mount hole of part C and moderately tighten the screw into part D. Once installed verify that the bearing turns freely.
4. Place a M3x12/16/18 FHCS screw through the hole in part C at the "nose" end and moderately tighten the screw into part D.
5. Install the Tensioner Arm onto the Tensioner Mnt using a 3x16/18mm FHCS screw. Tighten until snug and then back off until the arm rotates freely on the mount.
6. Place an M3 washer followed by the spring onto an M3x25/35/45mm SHCS screw and slide through the slotted hole in the bottom of the Tensioner Arm Assembly. Screw the SHCS screw into the heatset insert of the Tensioner Mnt. No tension should be on the spring at this point.

Remove
Support
C

D

E

ENRAGED RABBIT CARROT FEEDER (ERCF)

### TENSIONER ARM ASSEMBLY

ALTERNATE TENSIONER SCREW ORIENTATION

### ASSEMBLY INSTRUCTIONS

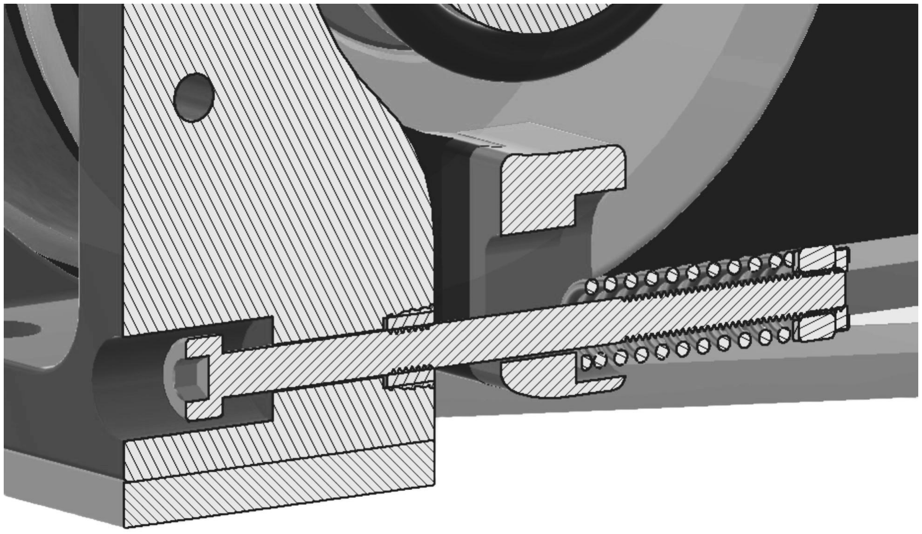
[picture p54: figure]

1. Insert the 3mm SHCS Tensioner screw from the bowden side of the rewinder through the heatset insert in the Tensioner Mount and the Tensioner Arm.
2. Insert the spring onto the Tensioner Screw.
3. Place an M3 washer followed by a lock nut, a nut with with threadlocker, or a heatset with threadlocker onto the Tensioner Screw to capture the spring.

If the orientation of your Filamentalist makes it difficult to access the tension adjustment screw you can reverse the 3mm SHCS Tensioner screw.

ENRAGED RABBIT CARROT FEEDER (ERCF)

### BASE ASSEMBLY

“Get back Jojo”
–The Beatles

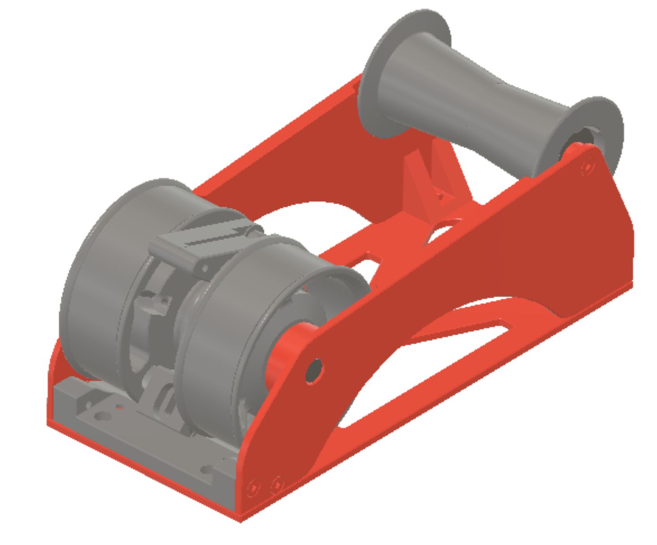
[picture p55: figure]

ENRAGED RABBIT CARROT FEEDER (ERCF)

### BASE ASSEMBLY

### EXPLODED VIEW

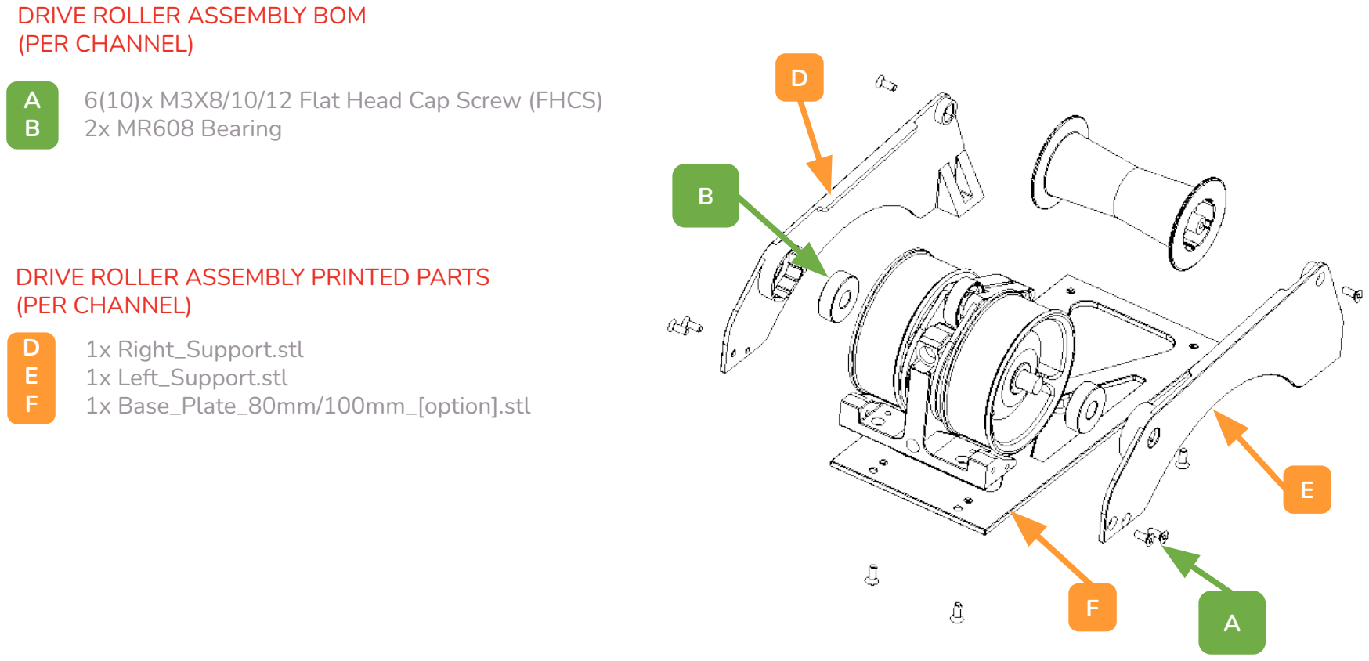
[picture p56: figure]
DRIVE ROLLER ASSEMBLY BOM (PER CHANNEL); 2x MR608 Bearing; 1x Right_Support.stl 1x Left_Support.stl 1x Base_Plate_80mm/100mm_[option].stl; DRIVE ROLLER ASSEMBLY PRINTED PARTS (PER CHANNEL)

6(10)x M3X8/10/12 Flat Head Cap Screw (FHCS)

ENRAGED RABBIT CARROT FEEDER (ERCF)

### BASE ASSEMBLY

### EXPLODED VIEW

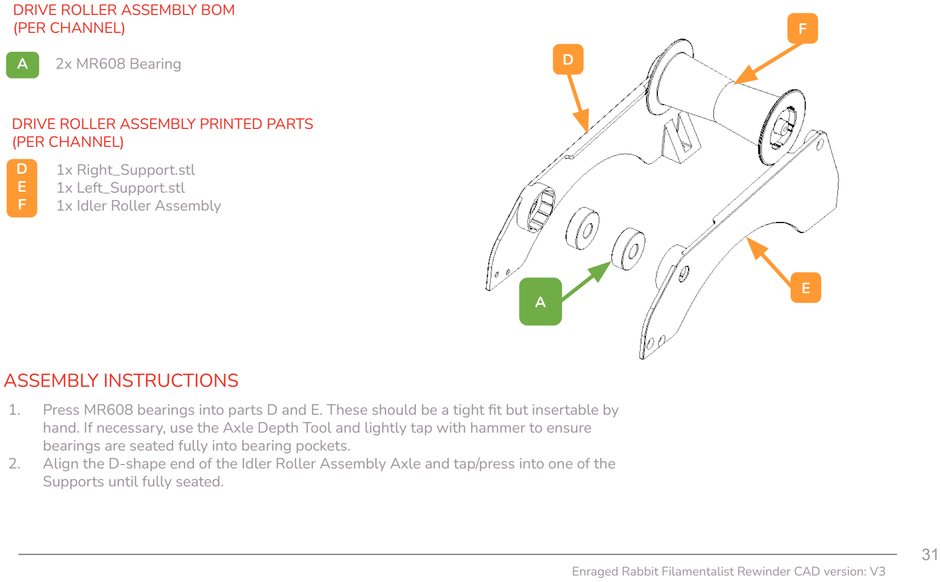
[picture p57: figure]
DRIVE ROLLER ASSEMBLY BOM (PER CHANNEL); 2x MR608 Bearing; 1x Right_Support.stl 1x Left_Support.stl 1x Idler Roller Assembly; DRIVE ROLLER ASSEMBLY PRINTED PARTS (PER CHANNEL); ASSEMBLY INSTRUCTIONS; Supports until fully seated.

1. Press MR608 bearings into parts D and E. These should be a tight fit but insertable by hand. If necessary, use the Axle Depth Tool and lightly tap with hammer to ensure bearings are seated fully into bearing pockets.
2. Align the D-shape end of the Idler Roller Assembly Axle and tap/press into one of the

ENRAGED RABBIT CARROT FEEDER (ERCF)

### BASE ASSEMBLY (continued)

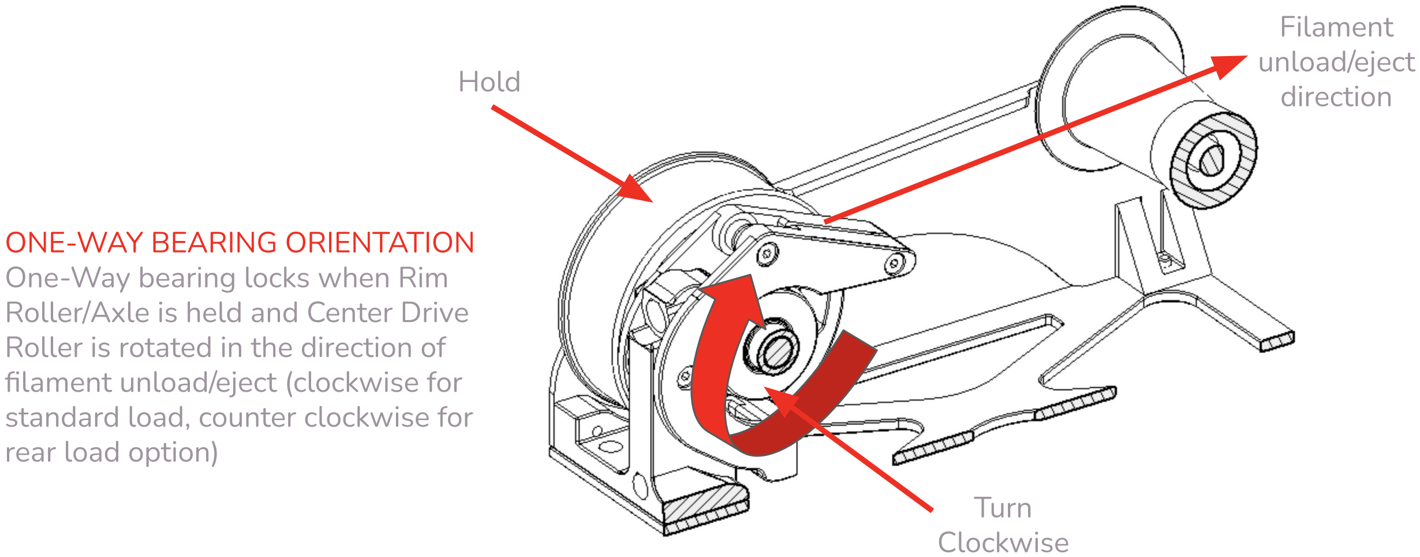
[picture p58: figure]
ONE-WAY BEARING ORIENTATION One-Way bearing locks when Rim Roller/Axle is held and Center Drive Roller is rotated in the direction of filament unload/eject (clockwise for standard load, counter clockwise for rear load option); Filament unload/eject direction Hold; Turn Clockwise

### ASSEMBLY INSTRUCTIONS (continued)

3. Insert Drive Roller Assembly axle into the MR608 bearing of the Support that has the Idler Roller Assembly installed on it.
3.1. IMPORTANT! Orient the Drive Roller Assembly so that the one-way bearing of the Center Drive Roller locks when rotated in the direction of a filament unload (if using the Tensioner Mount Rear Load option then the one-way bearing must be reversed and operate/lock in the counterclockwise direction with respect to the picture above).
4. Place Tensioner Assembly onto/over Drive Roller Assembly and Idler Roller onto Idler Roller Axle.

### BASE ASSEMBLY (continued)

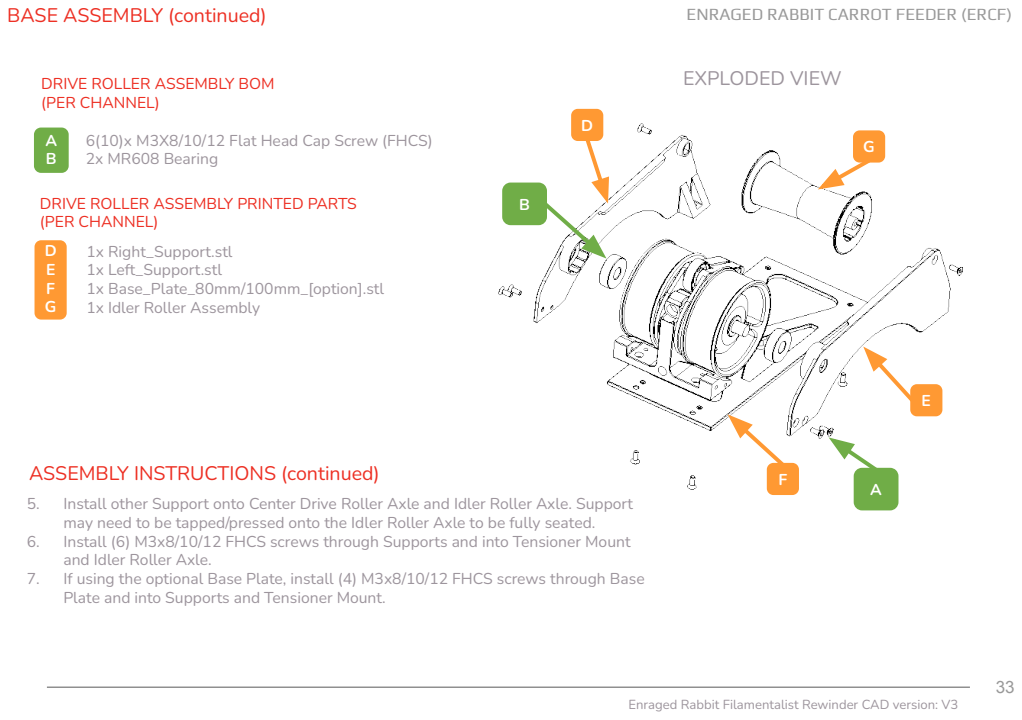
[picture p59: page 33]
DRIVE ROLLER ASSEMBLY BOM; EXPLODED VIEW; 1x Right_Support.stl 1x Left_Support.stl 1x Base_Plate_80mm/100mm_[option].stl 1x Idler Roller Assembly; DRIVE ROLLER ASSEMBLY PRINTED PARTS (PER CHANNEL)

ENRAGED RABBIT CARROT FEEDER (ERCF)

(PER CHANNEL)
6(10)x M3X8/10/12 Flat Head Cap Screw (FHCS)
2x MR608 Bearing

ASSEMBLY INSTRUCTIONS (continued)
5. Install other Support onto Center Drive Roller Axle and Idler Roller Axle. Support
may need to be tapped/pressed onto the Idler Roller Axle to be fully seated.
6. Install (6) M3x8/10/12 FHCS screws through Supports and into Tensioner Mount
and Idler Roller Axle.
7. If using the optional Base Plate, install (4) M3x8/10/12 FHCS screws through Base
Plate and into Supports and Tensioner Mount.

ENRAGED RABBIT CARROT FEEDER (ERCF)

### BASE ASSEMBLY (continued)

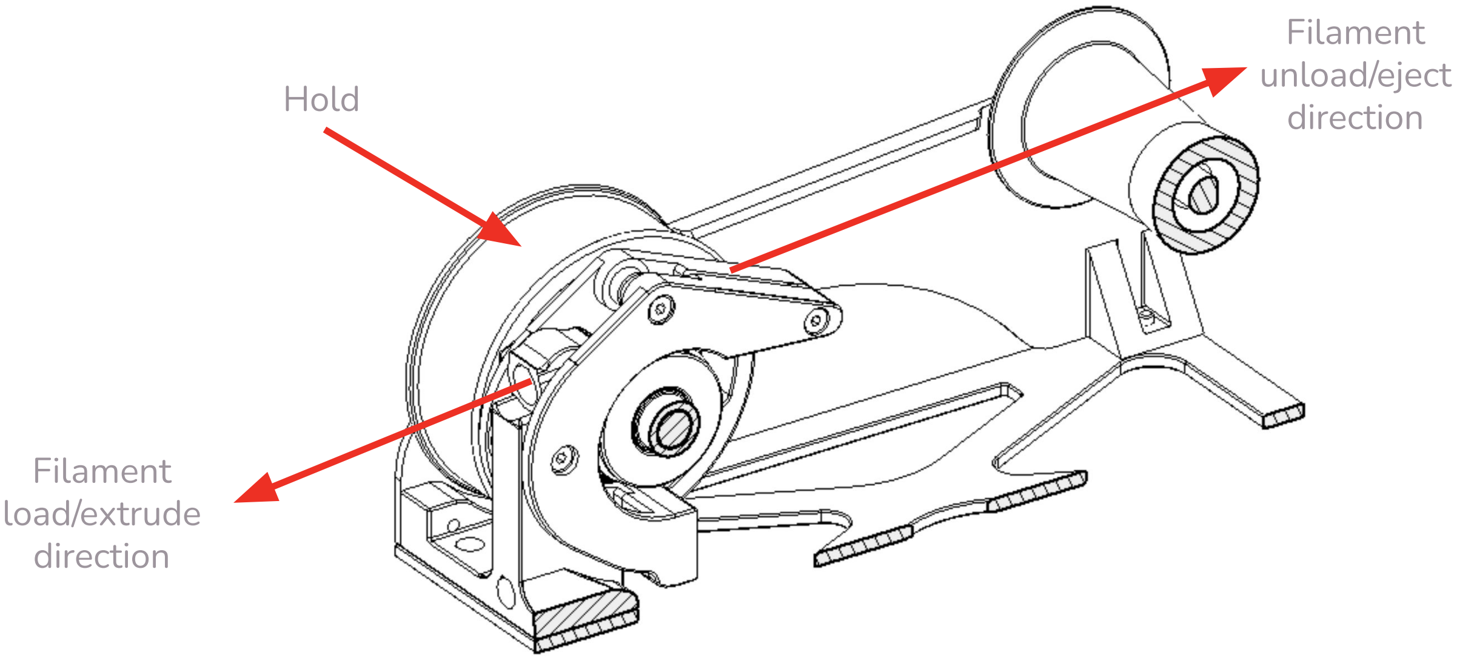
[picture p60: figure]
Filament unload/eject direction Hold; Filament load/extrude direction

8. Verify again that One-Way bearing is installed correctly. Insert a piece of filament through the filament path and tighten the Tensioner Screw to create medium spring tension.
9. Hold the center roller by placing your thumb/finger against the o-rings and try to pull the filament out in the eject direction.
10. The slip force/resistance against the filament should “light-to-moderate” (~0.2-0.3 kg or ~7-10 oz). Adjust the spring tensioner screw accordingly and err on the light side for a starting point.
11. While holding a Rim Roller with one hand, move the filament in the eject direction (see picture above). The Rim Roller should try to rotate against the pressure of your hand.
12. Continuing to hold a Rim Roller, move the filament in the load/extrude direction. The Rim Roller should not try to move and the Center Drive Roller should turn freely.

### ASSEMBLY INSTRUCTIONS (continued)

ENRAGED RABBIT CARROT FEEDER (ERCF)

### TUNING

### TUNING INSTRUCTIONS

Tune by setting the Tensioner Arm clamping force. The arm does not need an extreme amount of tension.
1. As a bench test (not connected to the MMU yet), load a spool of filament onto the rewinder and insert the filament through the o-ring/bearing interface and out the ECAS side of the Tensioner Mount.
2. Hold the center roller by placing your thumb/finger against the o-rings and try to pull the filament out in the eject direction.
3. The slip force/resistance should “light-to-moderate” (~0.2-0.3 kg or ~7-10 oz). Adjust the spring tensioner screw accordingly and err on the light side for a starting point.
4. Pull ~1m of filament in the load direction. Filament should stay tight on the spool (no loose loops). If loose loops form this indicates that the One-Way Bearing/Center Drive Assembly may be installed backwards (return to Center Drive Roller Assembly step), or the One-Way bearing is too tight on the Center Drive Roller Axle (see Filamentalist Troubleshooting Guide.). (https://github.com/SkiBikePrint/Filamentalist/blob/main/troubleshoot.md)
5. Starting with a tightly packed filament roll, push filament back onto the spool to simulate an MMU unload/eject. If loose filament is forming around the filament spool during unload, tighten the spring tensioning screw. If no loose filament is forming around the filament roll, gradually reduce the spring tension until loose filament starts to accumulate and then increase tension in ~1/2 screw turn increments until you feel you have the lightest tension that results in a tightly packed unload.
6. Initial tuning is complete and the rewinder can now be installed into your system. The same steps above can be followed after rewinder installation if additional tuning is required.

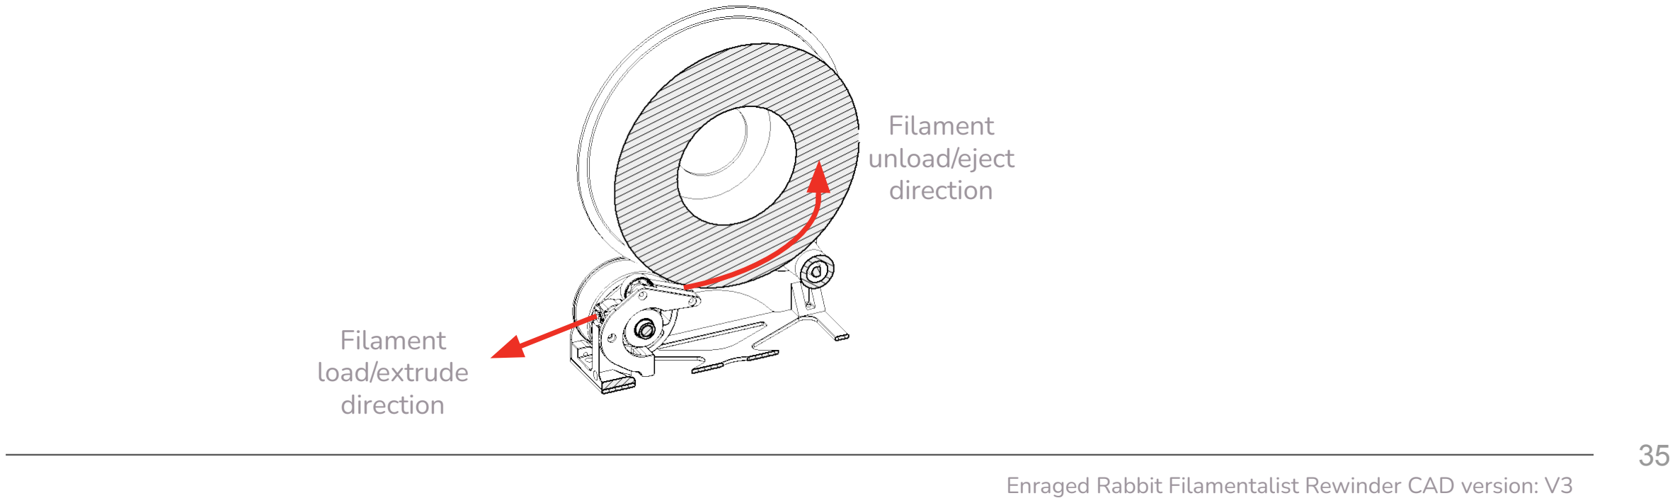
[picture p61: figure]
Filament unload/eject direction; Filament load/extrude direction

ENRAGED RABBIT CARROT FEEDER (ERCF)

### O-RING REPLACEMENT

You may never need to replace o-rings. Testing and extrapolation estimates that the wear-out point is ~5K cycles. The impact of o-ring wear-out can be reduced by periodically swapping highly used rewinders with low use rewinders in your line-up. Also, o-rings with grooves worn in them can be swapped with their opposing partners to present the unworn side/face to the filament to extend the life of a set. For o-ring replacement, FOLLOW THE STEPS BELOW:

1. Unscrew the (6) screws of the Right and Left Supports and remove them.
2. Remove the Drive Roller Assembly from under the Tension Mount Arms.
3. Unscrew the set screw(s) on one Rim Roller and remove it from the axle.
4. Slide the CDR Spacer and Center Drive Roller from the axle
5. Remove the old o-rings (a dental pic or small flat bladed screwdriver works great).
6. Install a pair of new o-rings.
7. Reinstall the Center Drive Roller and CDR Spacer back on the axle.
8. Install the Rim Roller back onto the axle.
a. Use Axle Depth Tool to set the correct distance of Rim Rollers from Axle end and tighten screw(s) firmly against Axle.
b. Confirm that the CDR spacers still freely spin on Axle with~0.5mm space between adjacent parts.
9. Verify that the Center Drive Roller Assembly/One-Way Bearing is in the correct orientation and reassembly the unit.

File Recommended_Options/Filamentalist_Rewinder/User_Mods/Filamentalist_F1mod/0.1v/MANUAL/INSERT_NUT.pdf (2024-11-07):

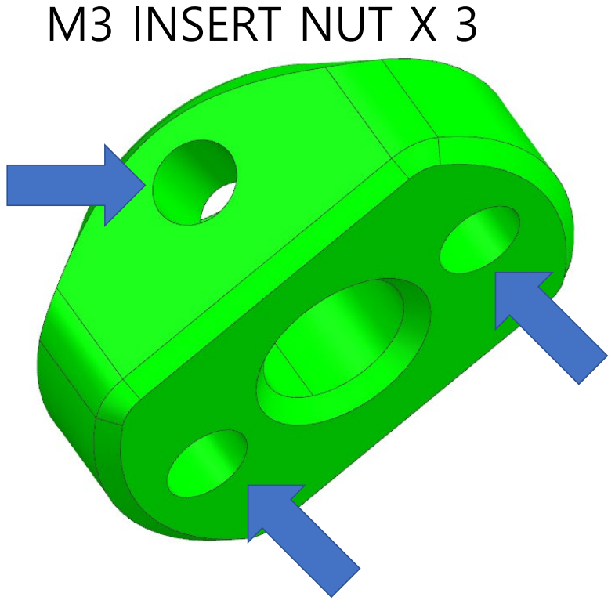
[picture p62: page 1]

M3 INSERT NUT X 3

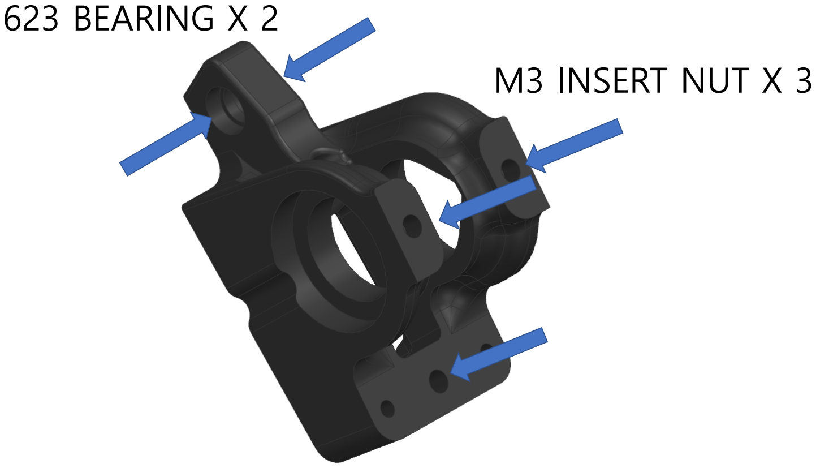
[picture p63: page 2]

M3 INSERT NUT X 3

623 BEARING X 2

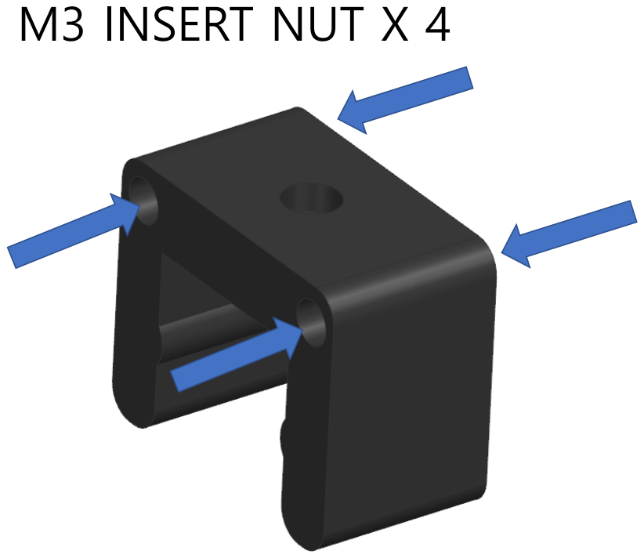
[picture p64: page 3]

M3 INSERT NUT X 4

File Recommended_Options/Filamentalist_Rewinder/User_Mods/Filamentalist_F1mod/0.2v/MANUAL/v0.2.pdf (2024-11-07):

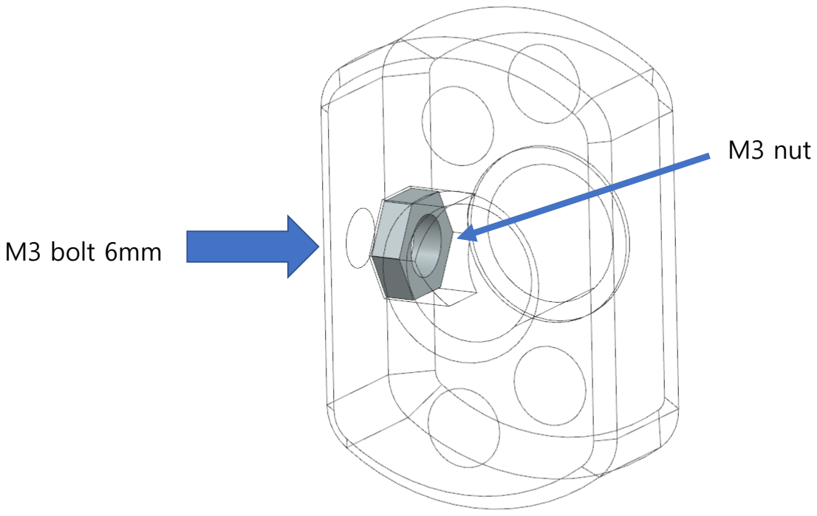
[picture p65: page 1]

M3 nut

M3 bolt 6mm

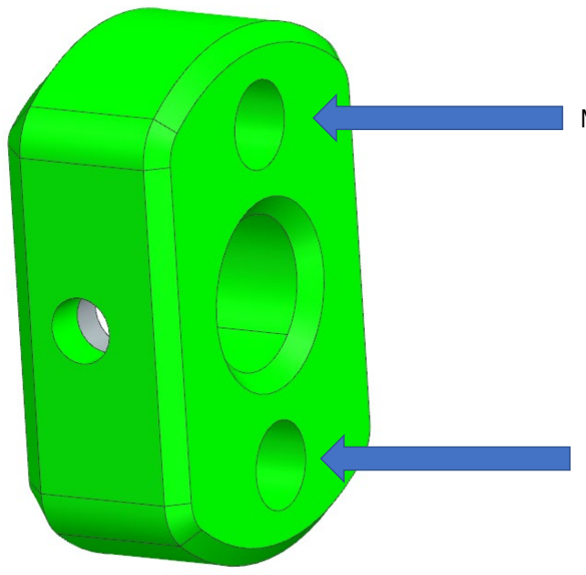
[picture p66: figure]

M3 insert nut

M3 insert nut

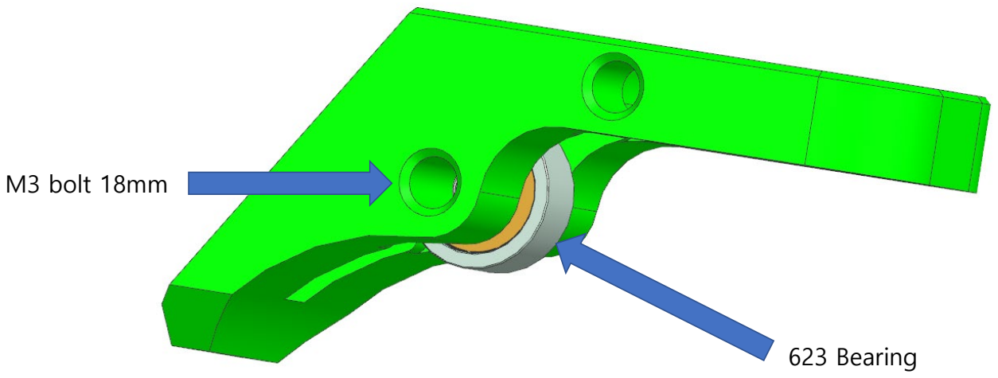
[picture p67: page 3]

623 Bearing

M3 bolt 18mm

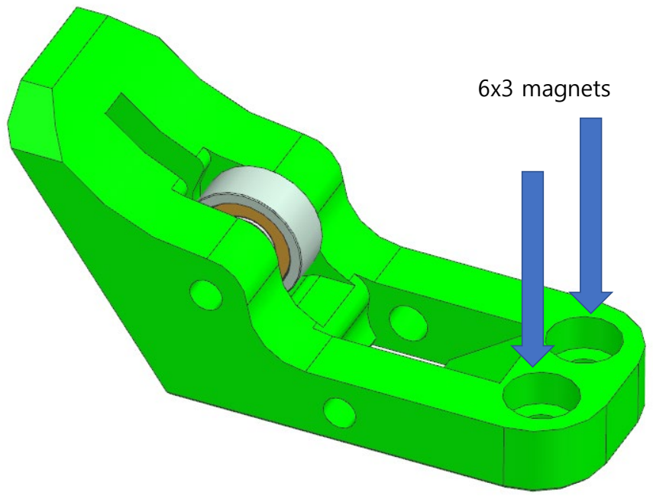
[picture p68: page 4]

6x3 magnets

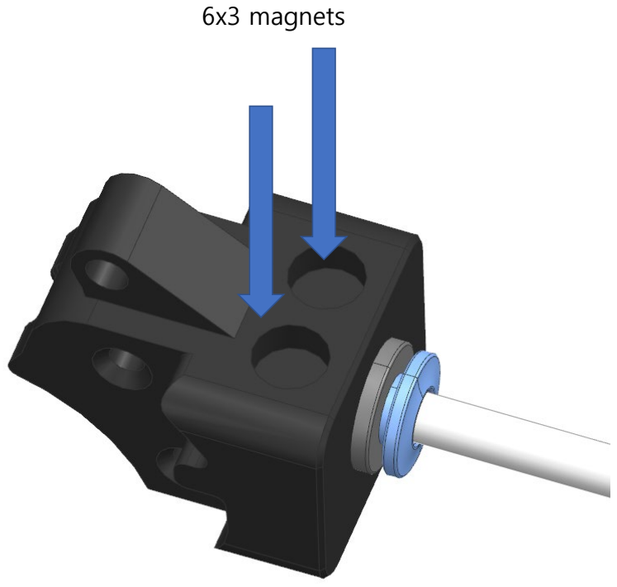
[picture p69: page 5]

6x3 magnets

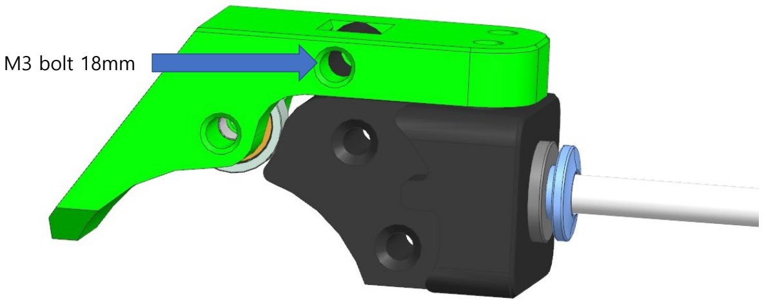
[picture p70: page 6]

M3 bolt 18mm

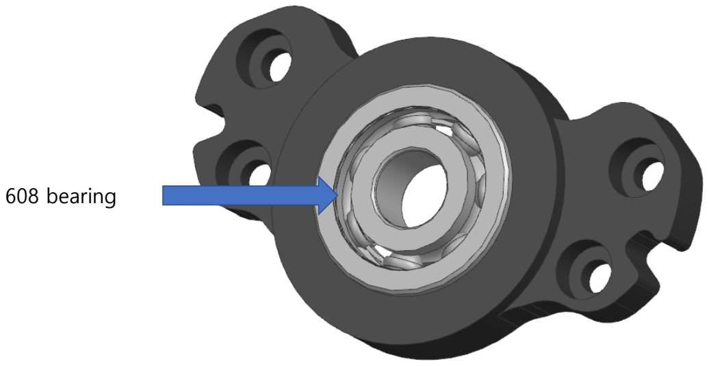
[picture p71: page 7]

608 bearing

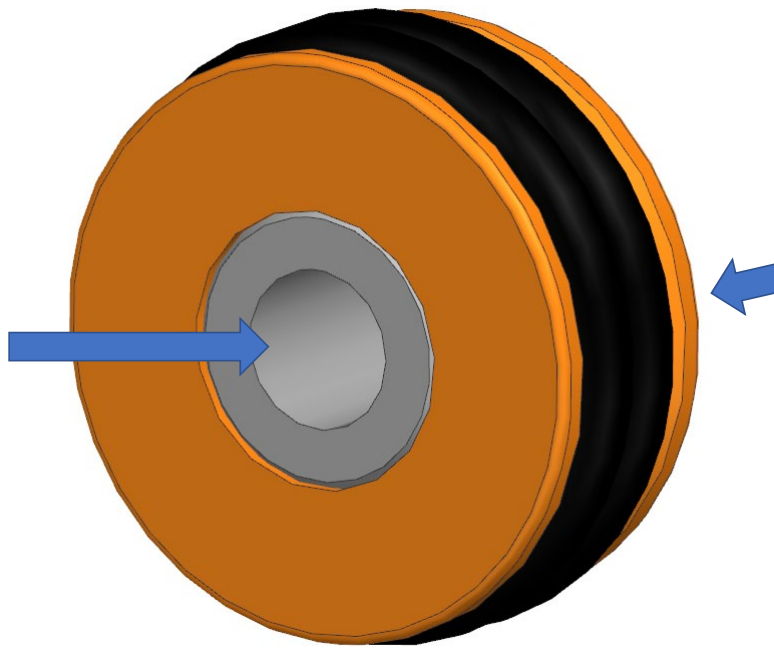
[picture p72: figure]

clutch bearing

O ring x 2

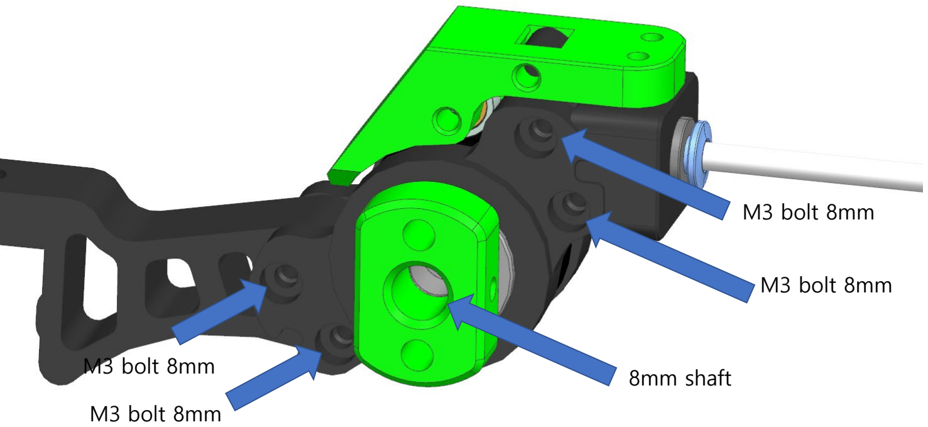
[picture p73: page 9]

8mm shaft

M3 bolt 8mm

M3 bolt 8mm

M3 bolt 8mm

M3 bolt 8mm

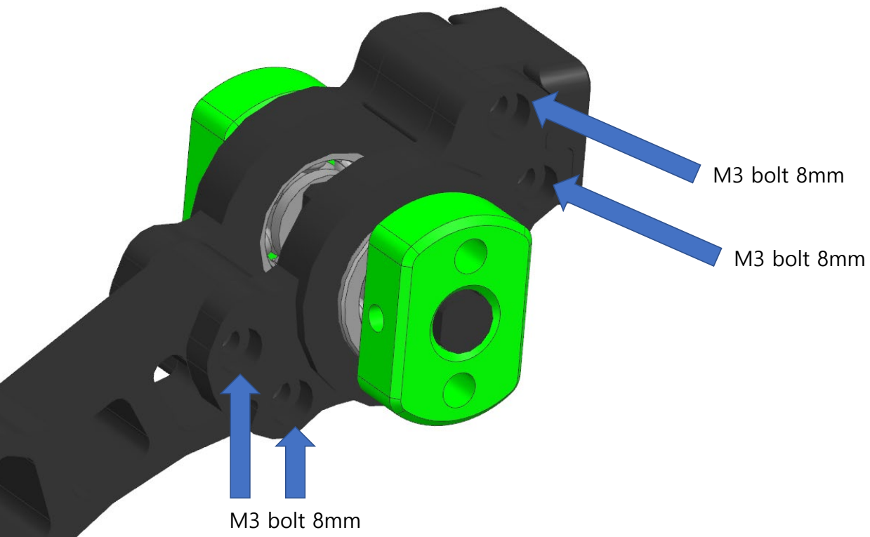
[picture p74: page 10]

M3 bolt 8mm

M3 bolt 8mm

M3 bolt 8mm

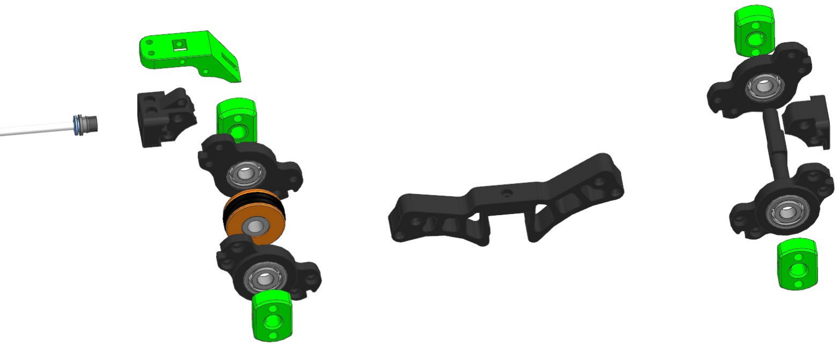
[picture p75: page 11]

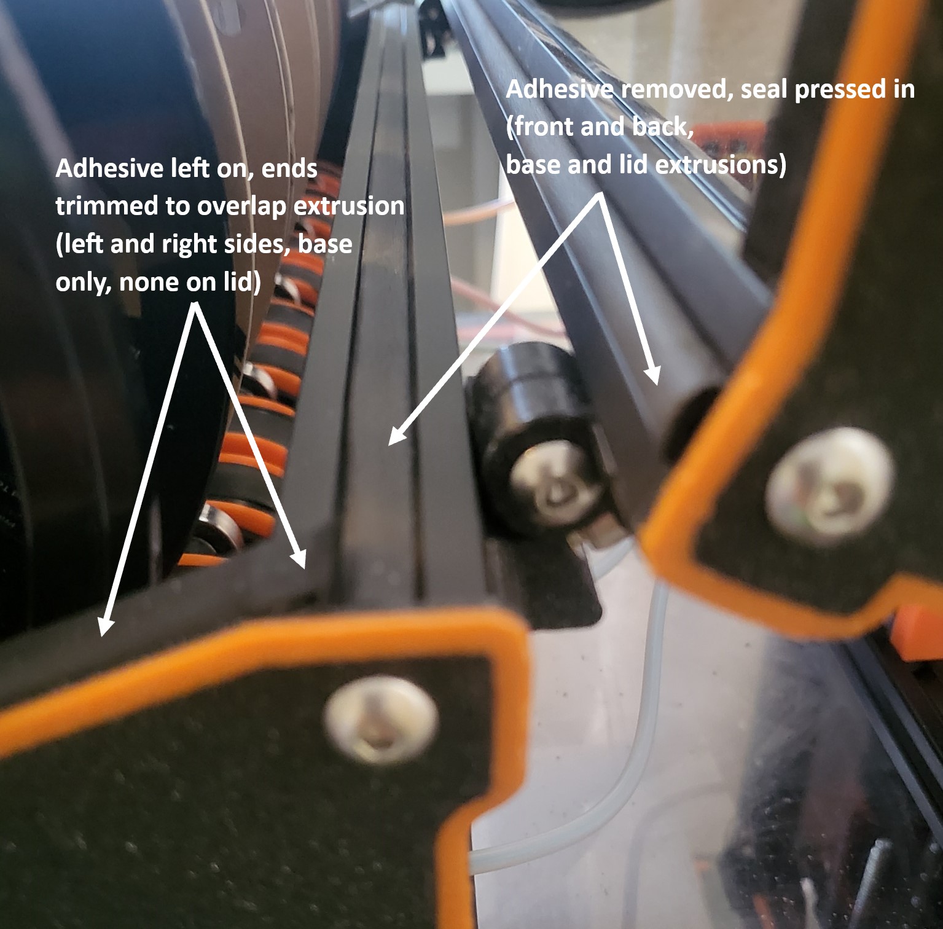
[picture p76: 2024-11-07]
Recommended_Options/Filamentalist_Rewinder/User_Mods/Filamentalist_Enclosure/Assets/Seal_Install_1.jpg

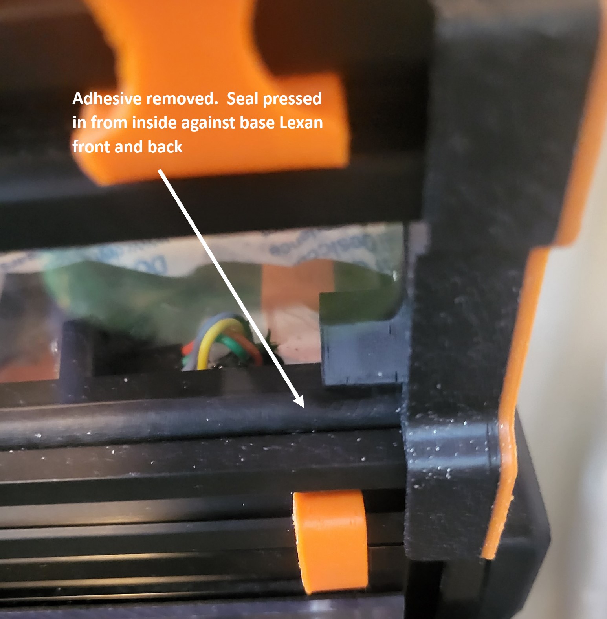
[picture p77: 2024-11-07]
Recommended_Options/Filamentalist_Rewinder/User_Mods/Filamentalist_Enclosure/Assets/Seal_Install_5.jpg

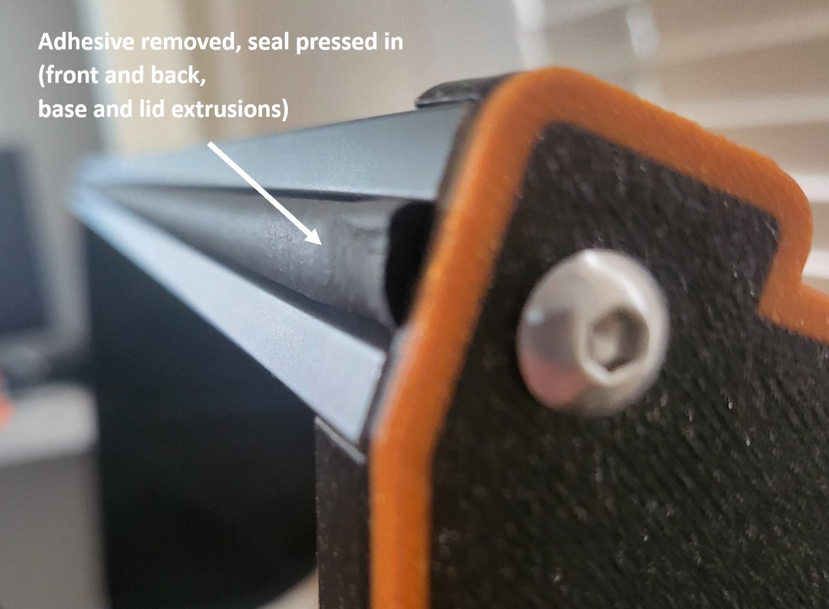
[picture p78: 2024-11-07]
Recommended_Options/Filamentalist_Rewinder/User_Mods/Filamentalist_Enclosure/Assets/Seal_Install_3.jpg

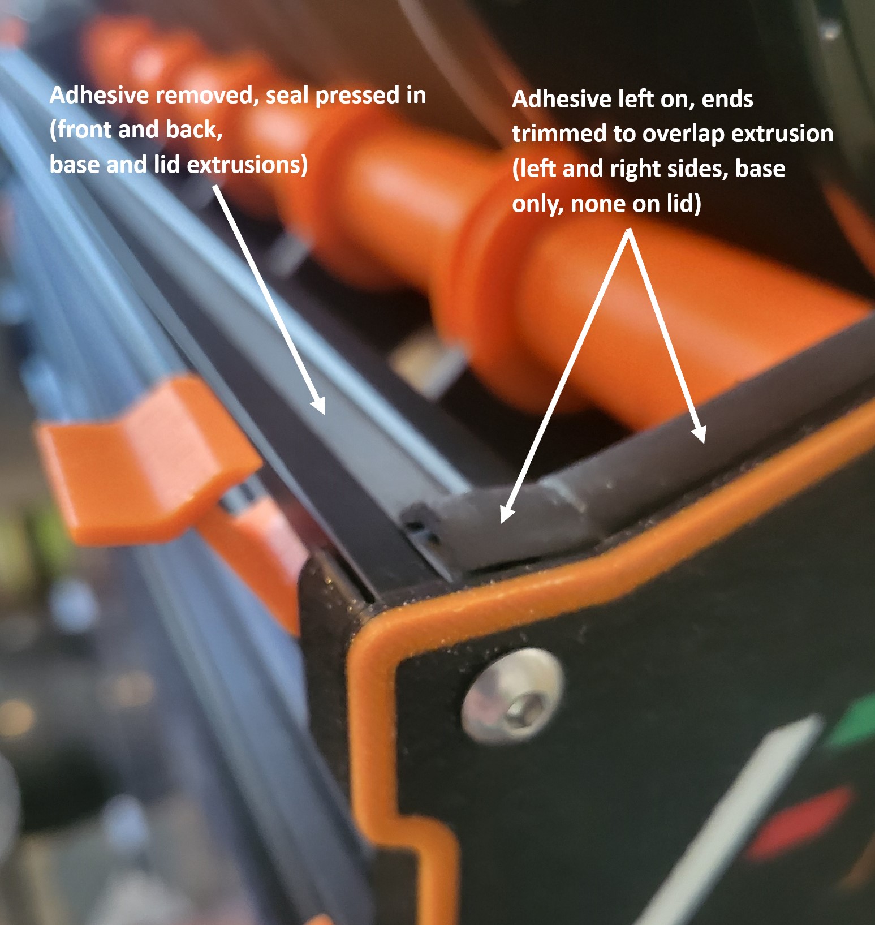
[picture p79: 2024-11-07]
Recommended_Options/Filamentalist_Rewinder/User_Mods/Filamentalist_Enclosure/Assets/Seal_Install_2.jpg

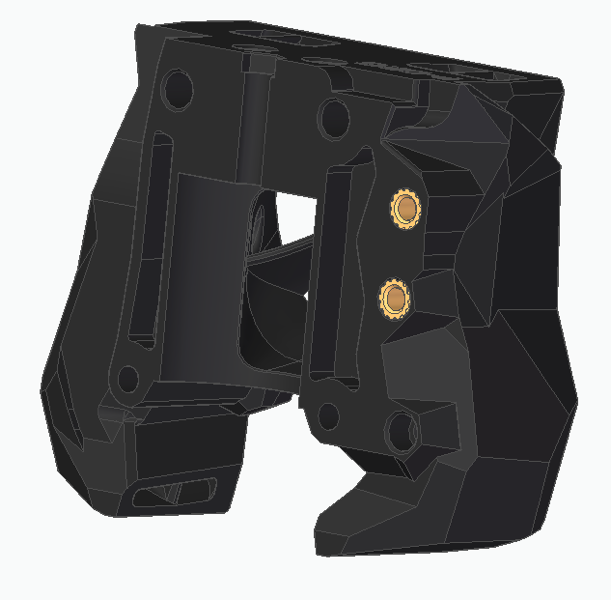
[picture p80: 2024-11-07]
Recommended_Options/ERF_Filament_Cutter/Assets/SB_Cutting_Printhead.png

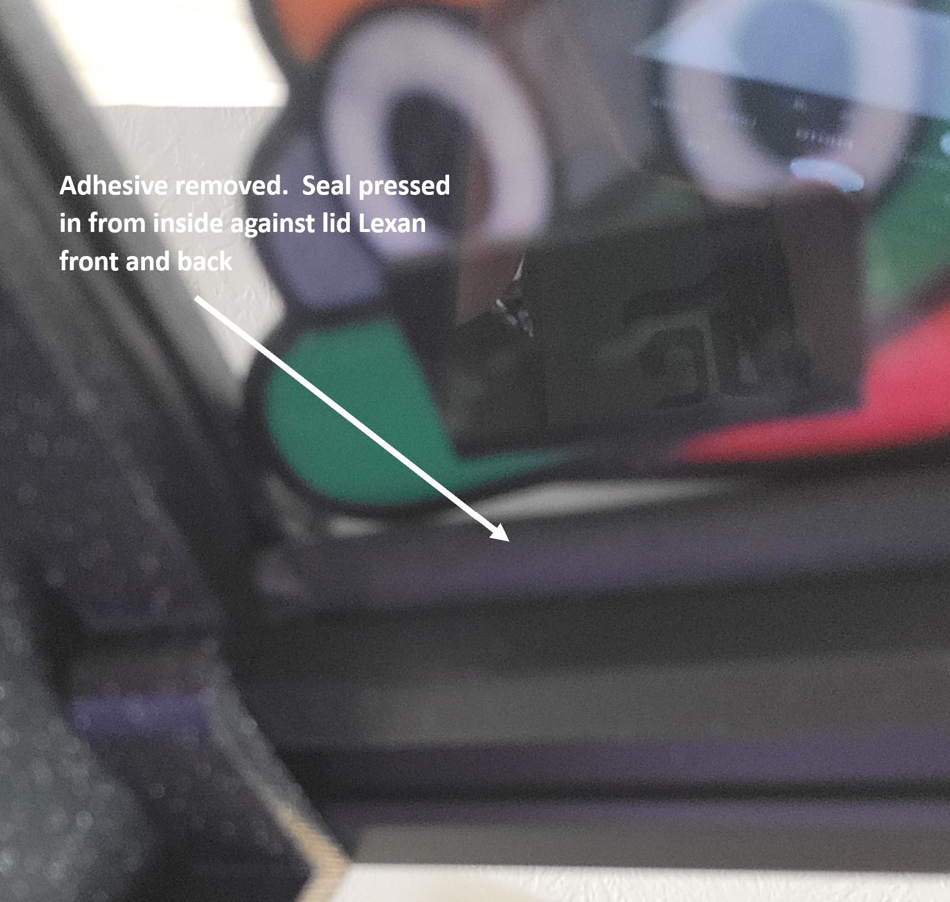
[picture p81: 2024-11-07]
Recommended_Options/Filamentalist_Rewinder/User_Mods/Filamentalist_Enclosure/Assets/Seal_Install_4.jpg

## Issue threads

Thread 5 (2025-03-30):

CAD files for the LED holder?

iMartyn, 2025-03-30:
There's some CAD files in the repo but nothing matching the [ERCF_8-channel_LED_Enclosure_by_SIBOOR.stl](https://github.com/Lzhikai/ERCF-V2-Accessories/blob/main/Siboor_Customized-kit_stl/ERCF_V2_Stls/Apron_Leds/ERCF_8-channel_LED_Enclosure_by_SIBOOR.stl) STL.

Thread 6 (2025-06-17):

CAD Files for older revision of selector with LED insert

smorenne, 2025-06-17:
Hello,

I am trying to install [EREC](https://github.com/kevinakasam/ERCF_Filament_Cutter) on my Siboor ERCF.

It seems I have an older revision of the kit where the following STL were present and required (git commit 1f57608):

ERCF_8 channel version_Stls/Selector（选择器）/Encoder_Left_V623ZZ_Exit_LED_insert.stl
ERCF_8 channel version_Stls/Selector（选择器）/Encoder_Left_V623ZZ_With_Exit_LED.stl
ERCF_8 channel version_Stls/Selector（选择器）/Encoder_Right_V623ZZ_With_Exit_LED.stl

Can you please upload or send the step/f3d files of these so that I can adapt them for the EREC?

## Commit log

2024-04-18 ERCF LED Panel.stl
2024-04-30 ERCF_8 channel version_Stls
    [Base_x8.stl, Bearing_Install_Tool.stl, Belt_Tensioner.stl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]
2024-09-11 update stl
    [Linear_Axis_10mm Idler_Block_SIBOOR.stl, Linear_Axis_9mm Idler_Block.stl]
2024-10-17 update new STL
    [Axle_8_Double_Thread.stl, Axle_Spacer_Standard_x8.stl, Bambu_Adapter.stl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]
